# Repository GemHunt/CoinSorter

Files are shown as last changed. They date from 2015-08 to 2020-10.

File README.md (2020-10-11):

# CoinSorter

CoinSorter is a low cost, open source, coin inspection system. It sorts coins by solenoid, on conveyors, by classifying images with deep learning based models using [Caffe](https://github.com/BVLC/caffe), OpenCV, Python, LMDB, and Arduino. The system uses an algorithm in which coin designs and features can be found with 1-5 labeled examples. This is done by augmenting the training image set with many different camera and lighting angles. 

Check out the video (https://www.youtube.com/watch?v=cwcn3tuXrv4)

**CoinSorter is the main repo. The project has many sub-repos:**
* Conveyors: [conveyors repo](https://github.com/GemHunt/conveyors)
* Lighting: [lighting-augmentation repo](https://github.com/GemHunt/lighting-augmentation)
* Hopper Metering: [hopper-metering-tool repo](https://github.com/GemHunt/hopper-metering-tool)
* Inital Scanning & Operation: [real-time-coin-id repo](https://github.com/GemHunt/real-time-coin-id)
* SAIL: Unsupervised Labeling: [sail repo](https://github.com/GemHunt/sail)
* Caffe fork needed for SAIL: [caffe repo](https://github.com/GemHunt/caffe)

**The Goal of CoinSorter is to be a:**

* Image collection system for a stand-alone automated coin grading & counterfeit detection app
* High speed coin scanning, inspection, and sorting system
* Tool for finding rare coins
* Study tool for the classification of images using deep learning.
* System costing less than $200 as a kit excluding the cost of the computer and optional GPU card and less than $50 in a quantity of 20 systems provided you have free access to a laser cutter.
* Low cost, real world example of an open high speed machine vision system that can be used as a starting point for handling, inspection, and manufacture of other small parts.

|Clear Belt & Cameras Removed| Scanning with a Center Cutout| Top and Bottom Camera Closeup|
| --- | --- | --- |
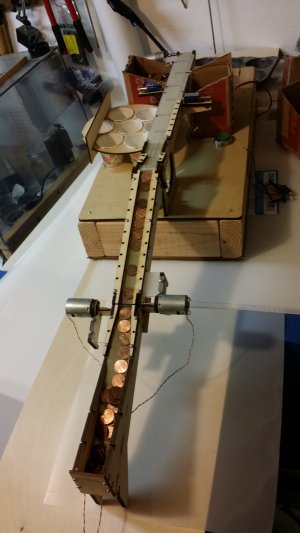
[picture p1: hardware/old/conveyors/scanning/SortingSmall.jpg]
Sorting
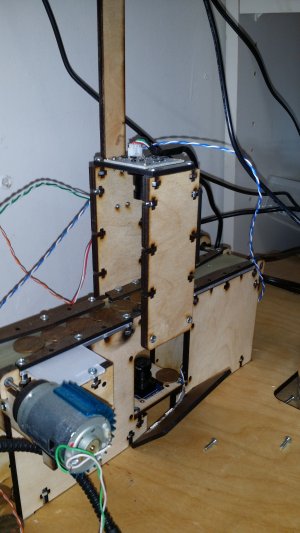
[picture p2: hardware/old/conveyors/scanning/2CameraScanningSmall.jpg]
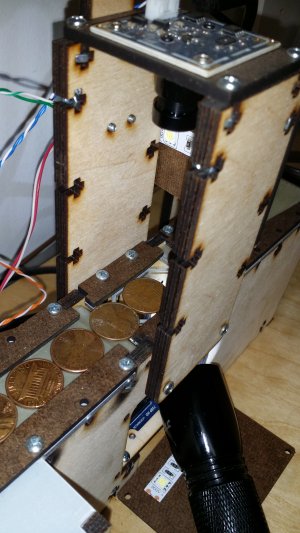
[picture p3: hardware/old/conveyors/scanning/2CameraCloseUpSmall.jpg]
||||

**Milestones & Short term goals & tasks:**
* GitHub milestones and issues are the best place to understand the project's past, present, and future. 
* In general the short term goal is to [sort 2 pennies a second by type, date and mintmark.](https://github.com/GemHunt/CoinSorter/issues/57)  
* Check out the [starting point issues](https://github.com/GemHunt/CoinSorter/labels/starting%20point) to see what is currently being worked on.
* For long term project direction [check out the issues for future milestones.](https://github.com/GemHunt/CoinSorter/milestones/Future%20Milestones) 

**Usage:**
* A new Python version is being planned.
* All C# code is being dropped from the project and will no long be maintained.   
* The new conveyors need to be documented and linked here, but in general everything is in [one Rhino 3D file.](https://github.com/GemHunt/CoinSorter/blob/master/hardware/conveyors/endMount/endMount.3dm)
* [View the old parts list and documentation](https://github.com/GemHunt/conveyors)

**How to Contribute & Participate**
* Buy and build the kit yourself. (I need to post the kit on eBay...)
* Work on, comment, and post new [issues.](https://github.com/GemHunt/CoinSorter/issues)
* If you have a laser cutter feel free to to build and sell systems yourself.
* If your into Caffe and don't want to post, just call me at 630-830-6640.

**Past Progress:**
* 2 working proof of concepts have been built proving Caffe & DIGITS is an excellent choice for coin image classification using small fully connected LeNet style networks.
* Over 20 prototype conveyors have been build each improving on the last design with around 150,000 coins imaged so far. 
* The full hardware setup is mature enough that others can start building and using it. 

**Detailed History:**
* The first proof of concept of this system used a C# project to capture images from a Canon Rebel camera and called MATLAB to preprocess them. A VB project was used to call DIGITS to classify the images and call a HP Power supply to drive a solenoid. These two projects have now been replaced. 

* The second proof of concept used C#, OpenCV, a webcam, Arduino solenoid control, and local classification with Caffe on Windows 10. Here is a [poster](https://github.com/GemHunt/CoinSorter/blob/master/docs/GTC%20Poster.pdf) and a [Power Point](https://github.com/GemHunt/CoinSorter/blob/master/docs/Deep%20Learning%20with%20Caffe%20%26%20DIGITS%20for%20Robotic.pptx) that describes the 2nd version. [You can download the second proof of concept release here.](https://github.com/GemHunt/CoinSorter/releases/tag/v0.2) 

* This first two groups of programs and scripts were just a quick proof of concept to show physical coin sorting. They sorted about 2 pennies a second, continuously. One solenoid and 2 physical bins are currently set up. Using Caffe it’s easy to distinguish between designs, orintation, and dates of coins. For example you can train a convolutional neural network (CNN, what Caffe uses) to determine if a coin image is heads vs tails or say recognize the state on a random US state quarter image. On one of the first models that was built Caffe could tell heads vs tails between US copper pennies 99.9% of the time. This can be done using using [DIGITS](https://github.com/NVIDIA/DIGITS) with default setting of AlexNet with no programming involved! In practice it's more efficient to use smaller image sizes and optimized networks. 

**In Review:**
* On the surface this system may look toy like and have a very narrow focus, but this is not true at all. You can take the basics of this system and use it for all sorts of very practical industrial uses. It’s not just sorting a handful of coins. It scales very quickly to tons of coins (or any parts for that matter). I have no doubt the system will get to the thousands of users range and be used for uses I could never envision. 

* Nothing remotely like it exists that is very low cost or open source. There are undocumented one off builds for all kinds of part handling. Probably the closest thing would be the open source pick and place machines. I have yet to see any personal or open source part handling systems that use the current crop of deep learning tools. MakerBot did have a conveyor on one of their machines, but this was a blind setup. Please let me know if you know about other, complete or not, documented open hardware machine vision systems

**Feel free to contact me if you have questions about this project.**

Thanks!  

Paul Krush

pkrush@Gemhunt.com

1-630-830-6640

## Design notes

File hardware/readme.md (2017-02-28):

This conveyor design is mostly for scanning. It's also to test out sorting. I have come to the conclusion that until conveyors are being build for sorting I don't know what they should look like. Initially scanning to learn how this all works is much different than deploying a conveyor to sort. 

The basic hardware of the conveyor is in the conveyors repo:https://github.com/GemHunt/conveyors

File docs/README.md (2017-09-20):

# CoinSorter

CoinSorter is an open source coin inspection system. It sorts coins by solenoid on conveyors by classifying images with models created using [Caffe](https://github.com/NVIDIA/caffe) &amp; [DIGITS](https://github.com/NVIDIA/DIGITS) and controlled with Python, OpenCV, and Arduino. 

**9/20/2017: This CoinSorter repo is out of date as new work is being doing in other repos. The project itself is still active. The biggest news is manual labeling has been eliminated! Designs and coin features sometimes can be found with only 1 example (One Shot Learning). The project has been rebuilt in a number of separate repos:**
* Conveyors: [conveyors repo](https://github.com/GemHunt/conveyors)
* Lighting: [lighting-augmentation repo](https://github.com/GemHunt/lighting-augmentation)
* Hopper Metering: [hopper-metering-tool repo](https://github.com/GemHunt/hopper-metering-tool)
* Inital Scanning & Operation: [real-time-coin-id repo](https://github.com/GemHunt/real-time-coin-id)
* SAIL: Unsupervised Labeling: [sail repo](https://github.com/GemHunt/sail)
* Caffe fork needed for SAIL: [caffe repo](https://github.com/GemHunt/caffe)

**The Goal of CoinSorter is to be a:**

* Image collection system for a stand-alone automated coin grading & counterfeit detection app
* High speed coin scanning, inspection, and sorting system
* Tool for finding rare coins
* Study tool for the classification of images using deep learning.
* System costing less than $200 as a kit excluding the cost of the computer and optional GPU card and less than $50 in a quantity of 20 systems provided you have free access to a laser cutter.
* Low cost, real world example of an open high speed machine vision system that can be used as a starting point for handling, inspection, and manufacture of other small parts.

|Clear Belt & Cameras Removed| Scanning with a Center Cutout| Top and Bottom Camera Closeup|
| --- | --- | --- |
|Sorting|Sorting|Sorting|

**Milestones & Short term goals & tasks:**
* GitHub milestones and issues are the best place to understand the project's past, present, and future. 
* In general the short term goal is to [sort 2 pennies a second by type, date and mintmark.](https://github.com/GemHunt/CoinSorter/issues/57)  
* Check out the [starting point issues](https://github.com/GemHunt/CoinSorter/labels/starting%20point) to see what is currently being worked on.
* For long term project direction [check out the issues for future milestones.](https://github.com/GemHunt/CoinSorter/milestones/Future%20Milestones) 

**Usage:**
* A new Python version is being planned.
* All C# code is being dropped from the project and will no long be maintained.   
* The new conveyors need to be documented and linked here, but in general everything is in [one Rhino 3D file.](https://github.com/GemHunt/CoinSorter/blob/master/hardware/conveyors/endMount/endMount.3dm)
* [View the old parts list and documentation](https://github.com/GemHunt/CoinSorter/tree/master/hardware/conveyors/conveyors.md) for the conveyors and the [old CAD files](https://github.com/GemHunt/CoinSorter/tree/master/hardware/conveyors/). 

**How to Contribute & Participate**
* Buy and build the kit yourself. (I need to post the kit on eBay...)
* Work on, comment, and post new [issues.](https://github.com/GemHunt/CoinSorter/issues)
* If you have a laser cutter feel free to to build and sell systems yourself.
* If your into Caffe and don't want to post, just call me at 630-830-6640.

**Past Progress:**
* 2 working proof of concepts have been built proving Caffe & DIGITS is an excellent choice for coin image classification using small fully connected LeNet style networks.
* Over 20 prototype conveyors have been build each improving on the last design with around 150,000 coins imaged so far. 
* The full hardware setup is mature enough that others can start building and using it. 

**Detailed History:**
* The first proof of concept of this system used a C# project to capture images from a Canon Rebel camera and called MATLAB to preprocess them. A VB project was used to call DIGITS to classify the images and call a HP Power supply to drive a solenoid. These two projects have now been replaced. 

* The second proof of concept used C#, OpenCV, a webcam, Arduino solenoid control, and local classification with Caffe on Windows 10. Here is a [poster](https://github.com/GemHunt/CoinSorter/blob/master/docs/GTC%20Poster.pdf) and a [Power Point](https://github.com/GemHunt/CoinSorter/blob/master/docs/Deep%20Learning%20with%20Caffe%20%26%20DIGITS%20for%20Robotic.pptx) that describes the 2nd version. [You can download the second proof of concept release here.](https://github.com/GemHunt/CoinSorter/releases/tag/v0.2) 

* This first two groups of programs and scripts were just a quick proof of concept to show physical coin sorting. They sorted about 2 pennies a second, continuously. One solenoid and 2 physical bins are currently set up. Using Caffe it’s easy to distinguish between designs, orintation, and dates of coins. For example you can train a convolutional neural network (CNN, what Caffe uses) to determine if a coin image is heads vs tails or say recognize the state on a random US state quarter image. On one of the first models that was built Caffe could tell heads vs tails between US copper pennies 99.9% of the time. This can be done using using [DIGITS](https://github.com/NVIDIA/DIGITS) with default setting of AlexNet with no programming involved! In practice it's more efficient to use smaller image sizes and optimized networks. 

**In Review:**
* On the surface this system may look toy like and have a very narrow focus, but this is not true at all. You can take the basics of this system and use it for all sorts of very practical industrial uses. It’s not just sorting a handful of coins. It scales very quickly to tons of coins (or any parts for that matter). I have no doubt the system will get to the thousands of users range and be used for uses I could never envision. 

* Nothing remotely like it exists that is very low cost or open source. There are undocumented one off builds for all kinds of part handling. Probably the closest thing would be the open source pick and place machines. I have yet to see any personal or open source part handling systems that use the current crop of deep learning tools. MakerBot did have a conveyor on one of their machines, but this was a blind setup. Please let me know if you know about other, complete or not, documented open hardware machine vision systems

**Feel free to contact me if you have questions about this project.**

Thanks!  

Paul Krush

pkrush@Gemhunt.com

1-630-830-6640

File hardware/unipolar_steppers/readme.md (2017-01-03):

Mitsumi m25sp-5n Unipolar Step Sequence
White:Orange:Red:Blue

This motor came from Jameco.
There is a tiny circuit board on the motor that you can cut the trace to power this with a bipolar driver. 

Notes to ordering better steppers:
Order bipolar wired motors
The 2 hole flange is much better for changing out motors, then the 370/385 DC motor style. 
These have a 5mm shaft. 8-10mm would be better. 
Have 4 stripped & tinned wires soldered on with assorted lengths.

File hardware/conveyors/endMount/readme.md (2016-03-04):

Conveyor Build Instructions

**Laser Cutting Tips:**
Push parts out from top (clean) side?
Rotating to top view is least confusing 
Mirror the side rail when cutting. 
Standard way to rotate to top views: 
	If you want to mirror flip the angle. 
If drawings are in Right view:
In front view, rotate, c    20, 0    90    enter - enter
If drawings are in Front view
In right view, rotate, c    0, 0    -90    enter - enter
Then invert & change object layer

Assembly Tips:
Nuts go into the clean (non-charred) side better. 
Motor & solenoid have M3 8mm screws
Horizontal solenoid plate screws & guide screws are 5/8” 4-40
Finger guides are 4# 3/8” sheet metal screws for now. 
All other screws are ½” 4-40.

If a nut gets stuck squeezing between 2 coins helps. 
Only snug screws until everything it together, then finish tightening. 

Make a Belt:
The glossy side should be the inside on the belt. The mat side is stickier. 
Cut 30mm wide belt:
	20cm Feeder/scanner Conveyor
	22cm short conveyor
	44.5cm hopper & accumulator conveyors
	104cm scanning conveyor

Heat seal (bond) smooth side in (Bright lighting helps)
I use an 8" $25 heat sealer for poly bags with a 2mm element.(3mm would be better)(A custom bonding rig would be nicer).
Scotch tape a 1mm overlap. 
Turn it inside out so the tape side is opposite the heating element before heat sealing. 
Heat seal 2 times to get the both side of the 1mm whole seam for .3mm thick
Heat seal 1 time for .15mm thick 
	On the dial I use a 2 setting for 0.15mm and 4.5 setting for 0.3mm
Remove Tape
Try not to heat seal a single layer area as this will thin it out. 
The clear belting is sticky. I sand all top plates with 220 sand paper. I wounder what grit is the best. 

Assembly Instructions:
	Put the 58mm shaft on the motor:
	Add the 17mm tubing coupling to the motor shaft. 
	Press 7mm on the motor (most of the way) 
	Add the 58mm 2mm shaft to this tubing, pressing about 7mm on. 
	There should be about a 2mm of tubing in the middle. 
Mount the motor:
To the Motor Rail 
With M3x.5 x 8mm long screws.
Cleaner side to the motor face. 
Screw on top plate to motor rail
Add solenoid plate to motor rail with one 5/8” screw
Add Middle Rail to top plate with 2 screws

Change this: it’s easier to then put on shafts, then belt, then side rail. 

If using guides:	
Add them with three 5/8” screws instead of two ½” screws
Guides need shim washers between the top plate and the guide
Add Side Rail to top plate with 2 screws
If using guides:	
Add them with three 5/8” screws instead of two ½” screws
Guides need shim washers between the top plate and the guide
Tighten guides with guide spacer in-between. 
Add shorter 42mm long 2mm shaft with 3/16 spacer pulleys:
	2 longer spacers on the end, and one shorter spacer in the middle. 
Put the belt on.
Add motor end plate
Add end plate
Final screw tightening:
Squeeze the side rails together when tightening the end plates. 
Don’t tighten top plate super tight as it will crown. 

Belt change:
Take off the end plates. 
Find a way to make it so you don’t have to take off the end plates? 
3 ½ minutes to change the belt with taking the end plates off. 
Squeeze the side rails together when tightening the end plates.

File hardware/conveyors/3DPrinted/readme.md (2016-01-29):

I don't think I will use this 3D Printed style again. The laser cut version is simpler and quicker to make. 

**Three types of conveyor ends have been used successfully:**
* Motor end in ¾” MDF
* Pulley end in ¾ MDF
* Pulley end in ¼ MDF

These conveyors built from ¾” frames have turned out way better than I thought they would. I first used 1mm thick belting at 100RPM and this was a bit under-powered. All the power is used to move the thicker belt under tension. It would move a full gallon of milk(3+ kilos) with no issues. 

With the 0.15mm thick belting that is currently be used the motors can be smaller, especially if you put in ball bearings. 

**Motor end in ¾” MDF Parts:**
* 25MM Gear motor, 4mm shaft 100-1000RPM
* 2 motor mount screws: M3-0.5 6 mm screws
* 3D printed gearbox bracket
* 3D printed D-coupling to take motor 4mm ID “D” to ¼” OD
* Coupling: Polyurethane Tubing, ½” OD, ¼” ID. 
* Coupling: Zip/cable Ties: 4”
* 75mm long ¼” steel shaft
* 35 mm long 3D printed pulley. 22mm diameter. 
* Drilled with “D”0.246” drill to press fit on ¼” shaft
* 2 3D printed Pulley Holders. 
* 2 Bushings: stock nylon shoulder spacers ½” Long, ¼” ID, 5/16” ID, ½” ID Flange
* 3 8” zip/cable ties hold on the gearbox bracket & pulley holders

**Pulley end in ¾ MDF**
* Same as motor side, except 60mm long shaft. 

**Pulley end in ¼” MDF:**
* Pulley end ¼” is 60mm wide
* 1/8” steel shaft, 60mm long
* 4 ¼” diameter nylon spacers, 1/8” hole, ½” long, Center spacer has tape to make it crown. 
* Wood is cutout for the pulleys
* Remaining wood is drilled 1/8”
* It’s pretty crude and fragile, but once it starts working I have yet to see fail. 
* It’s easy to drill so the shaft is not straight. Then the belt walks to one side. 
* In the pictures below the belt walked to one side anyway. It just did not matter. 

**Conveyor Belt:**
* 30mm wide, 0.15mm thick Polyurethane
* Normally used for sealing fabric together, under garment strapping, etc.
* Sold as “TPU Tape” on Aliexpress.com
* Length wise sized 5% under  
* Bonded together with a standard impulse heat sealer used for sealing poly plastic bags. 

**Speed Controllers:**
* The first proof of concept had 24V power stepped down to 5 to 18 volts for the 12V motors with DC-DC LM2596 modules. This are really common, $1-2 on eBay, Amazon, etc. The system moving coins with motors running at 5-7 volts is surprisingly quiet with the coin hopper turned off. 

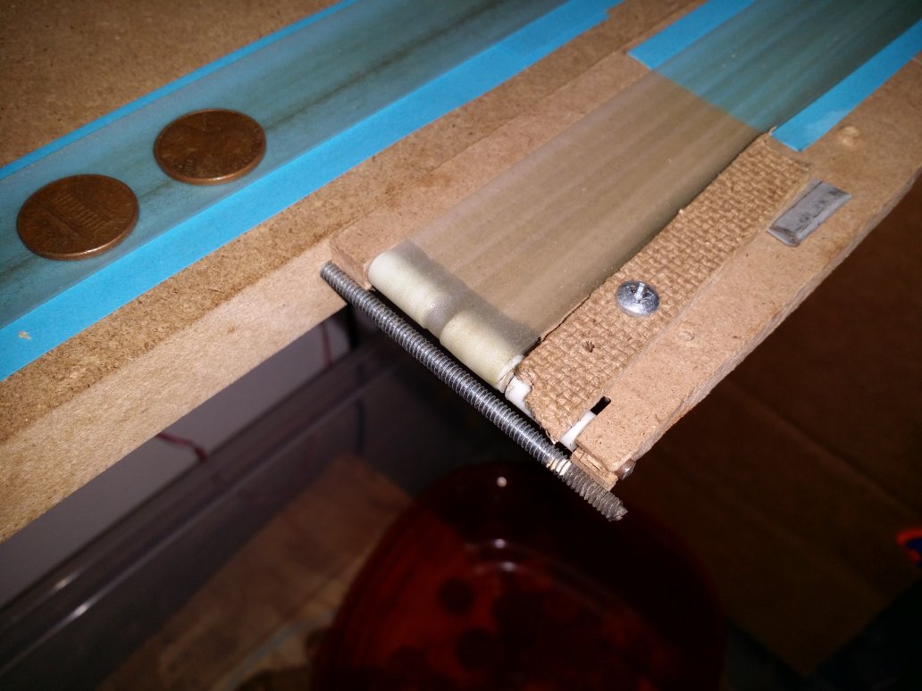
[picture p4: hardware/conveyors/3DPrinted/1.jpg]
Image of Conveyor 1

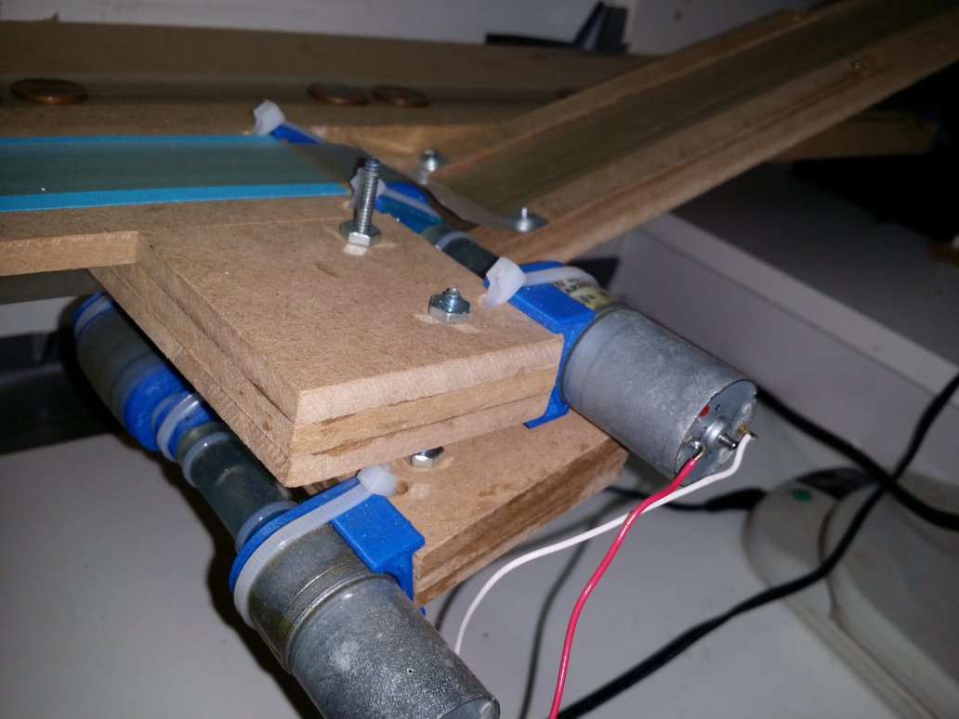
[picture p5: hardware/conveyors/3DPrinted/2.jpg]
Image of Conveyor 2

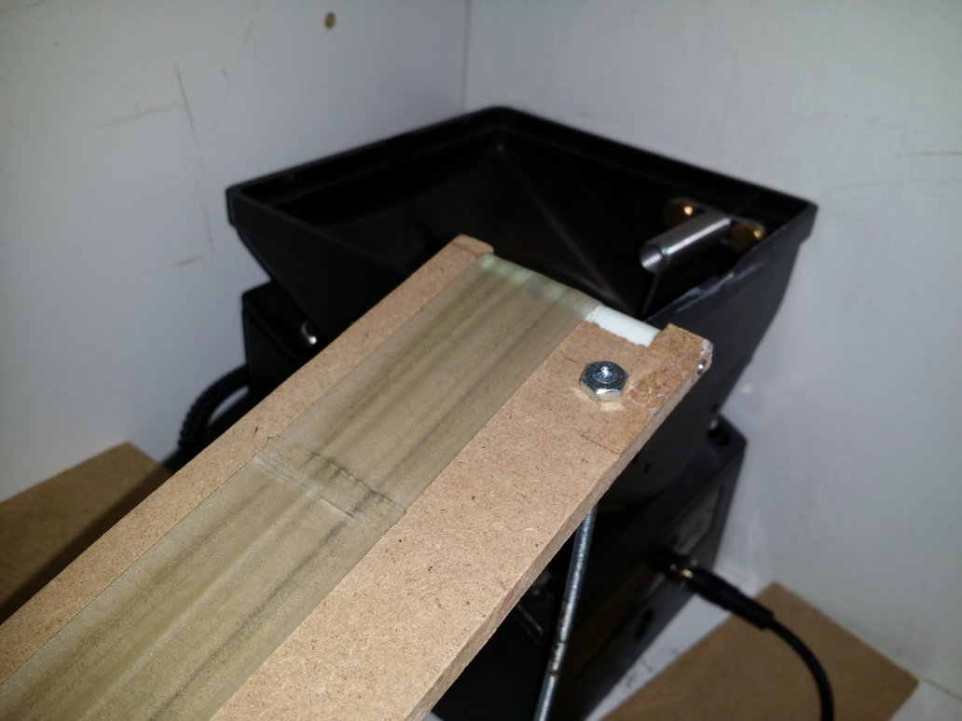
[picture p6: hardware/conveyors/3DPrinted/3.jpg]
Image of Conveyor 3

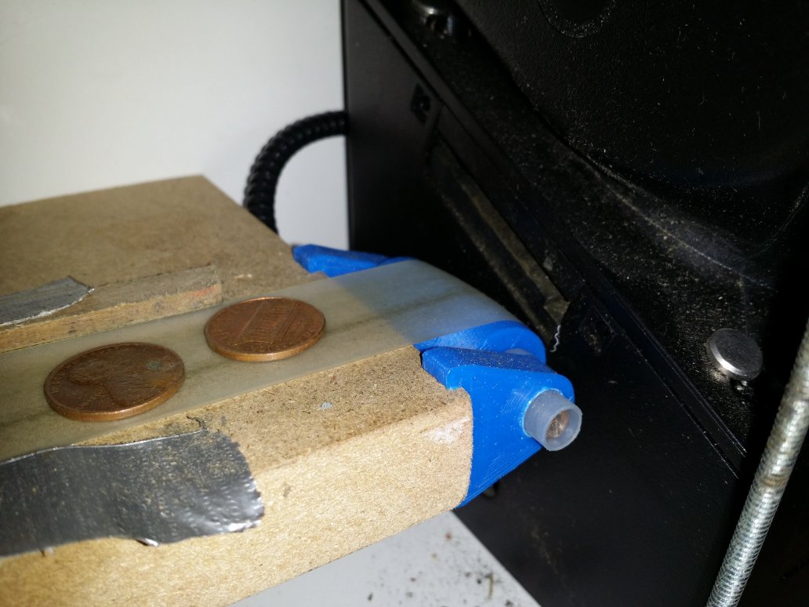
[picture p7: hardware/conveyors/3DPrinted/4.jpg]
Image of Conveyor 4

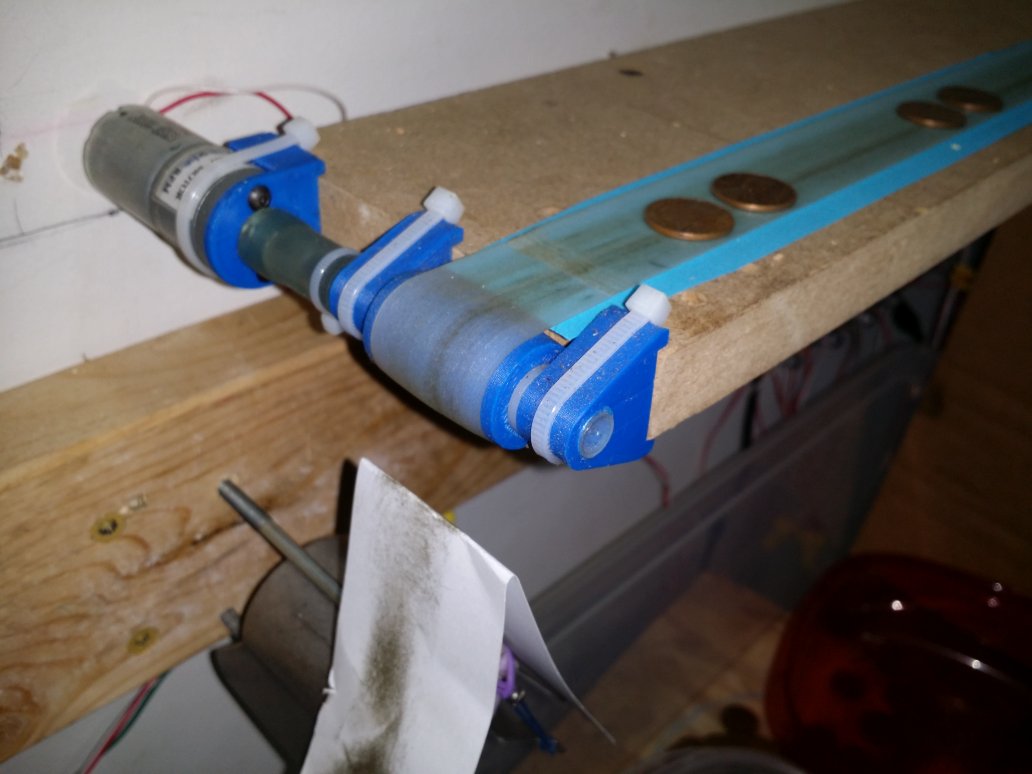
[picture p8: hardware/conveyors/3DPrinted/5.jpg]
Image of Conveyor 5


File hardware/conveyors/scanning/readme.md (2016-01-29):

This is the start of the scanning conveyor

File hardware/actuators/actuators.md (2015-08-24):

**Proof of Concept Actuator:**

A Rotary Flapper Solenoid:
* A USPS surplus RAM MFG CO ROTARY SOLENOID ACTUATOR part 40R10102
* This is too big and I don't recommend it. 

What should be used?
Solenoids certainly seems the most logical.
Such as low cost push solenoids to knock coins off the belt:
* 5mm travel?
* Maybe some type of foot it's more then just the rod end, but try without a foot first.
* Rotary solenoids seems like a good idea, but I have not seen many.

Motors you could sort to more than one bin:
* RC servos are so common and easy to control. 
* Cheap stepper motors might not be a bad idea.

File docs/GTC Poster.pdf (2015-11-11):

# High Speed Coin Sorting With Convolutional Neural Networks

# Paul Krush

https://github.com/GemHunt/CoinSorter

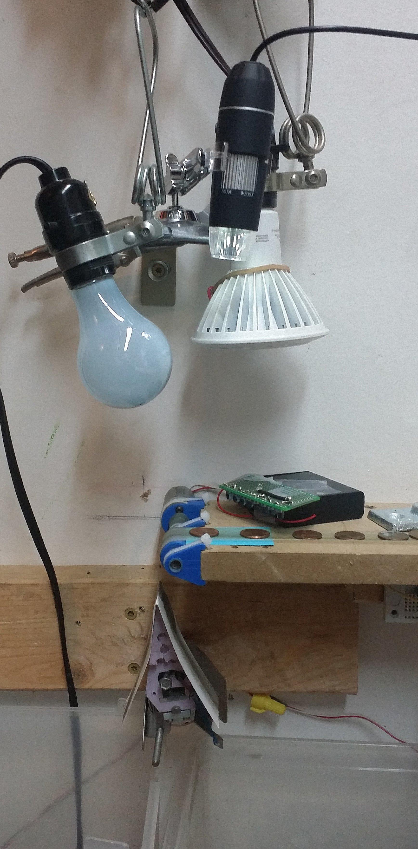
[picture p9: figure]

## Introduction:

The goal of this project is to physically sort pennies by date very quickly with low cost open source hardware & software.

Caffe CNN: Coin date classification, a stock cifar10 network, 32x32 color

Caffe CNN: Coin orientation classification (images rotated to create 360 different categories) LeNet with an additional set of conv & pooling layers, 2x output, 64x64 gray

Caffe CNN: Coin design classification (Heads vs Tails vs Other…) LeNet with an additional set of conv & pooling layers. 2x output, 60x60 gray, 12x rotational augmentation

Caffe CNN: Detection of the 5% poorly cropped coins with a stock cifar10 network, 32x32 color

OpenCV: Coin image crop from contour detection

OpenCV: Threshold in Cr component of the YCbCr space

OpenCV: Removal of skew (caused by coin moving at high speed)

OpenCV: Image captured from webcam, triggered by IR sensor from Arduino

## Image Processing Pipeline:

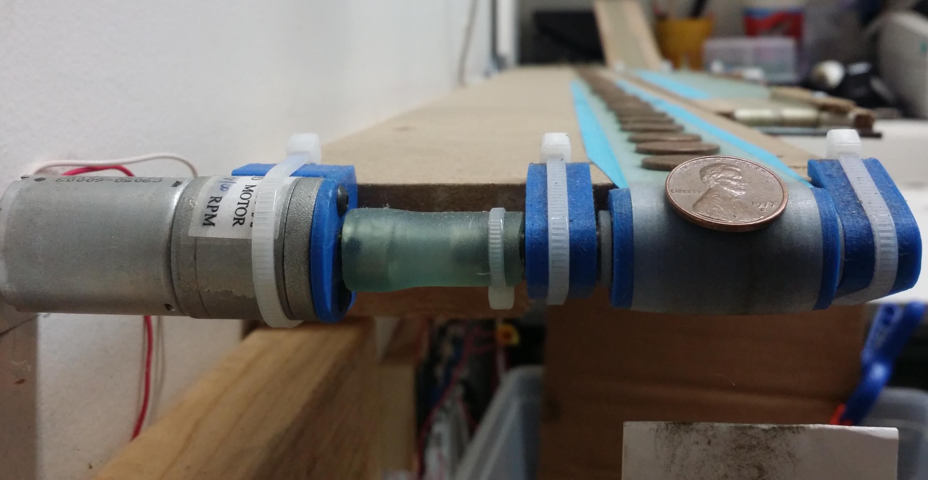
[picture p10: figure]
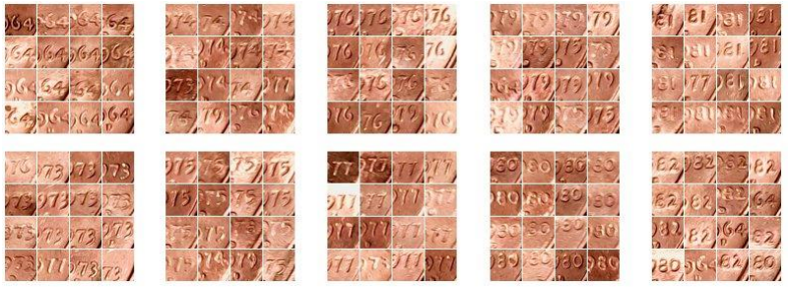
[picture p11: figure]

## Future Work:

One of the holy grails of modern numismatics is to discover new types of coin varieties and mint-made errors. Automatically correlating coin regions and features by date and mint mark is the next logical milestone to archive this. Capturing both sides of the coin will be a requirement to do this.

## Next Steps:

Camera & lighting
needs to be fixtured
and standardized.
Four different lighting
and camera setups
have been used so far.
Accuracy drops
drastically after the
camera type, position,
lens, or lighting
changes. Cropping
issues need to be fixed
and matched to the
possible new camera.

## Motivation:

To learn about machine vision and get experience with the full life cycle of a machine vision product. To gain experience with the current crop of deep learning tools and their use of NVidia GPUs.
So the tail wags the dog… The field of high speed coin classification was chosen because of current GPU computational efficiency over CPUs and more importantly future GPU computational scalability.

## Hardware & Software Mechanics:

At this point the system is just a quick proof of concept to show physical coin sorting. It sorts about 2 pennies a second, continuously. One solenoid and 2 physical bins are currently set up. It uses C#, OpenCV for image preprocessing, a cheap microscope webcam, an Arduino for solenoid control, SQLite, and local classification with Caffe complied on Windows 10. Model training is done on a Linux server, either local or AWS, with Caffe & DIGITS.
Coins are metered by an off-the-shelf coin hopper. Conveyor hardware is 3D printed ABS. Conveyor belting is undergarment strapping. (0.15mm “TPU Tape”)

## Results:

Start to finish preliminary accuracy is around 70 percent. Expected accuracy is much higher. Most of the error at this point is due to using a very small training set. Simple improvements can be made throughout the pipeline.

## Conclusion:

So far accuracy is higher than expected which is great. Unfortunately the project is taking a lot longer than expected. Computational requirements are much lower than expected, which ironically does not fulfill the stated goal of needing a GPU for classification! Of course this is a good problem to have and leaves the door wide open for more complex work in the future.

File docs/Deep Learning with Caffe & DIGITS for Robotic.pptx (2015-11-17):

## Deep Learning with Caffe & DIGITS for Robotic Coin Collecting

https://github.com/GemHunt/CoinSorter

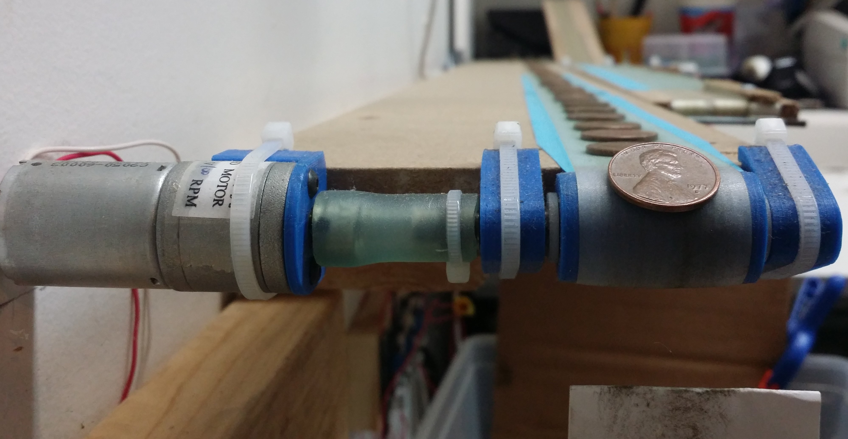
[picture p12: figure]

## Who am I?

- Software developer and mechatronics engineer
- Mechatronics?
- GemHunt.com: Am I going the startup route? Again?
- Live Carol Stream with my wife and two boys

## Questions? Comments? Feel free to Stop me! Or just Post a GitHub issue github.com/GemHunt/CoinSorter

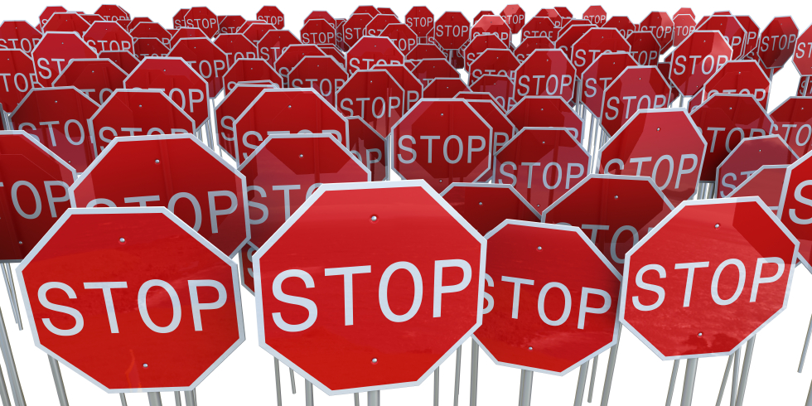
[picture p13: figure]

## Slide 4

Start Time | Minutes
7:00 PM | 10 | UniForum Intro
7:10 PM | 5 | Presentation Intro
7:15 PM | 5 | Check out the GitHub: Project Goals/Milestones
7:20 PM | 5 | What is Deep Learning?
7:25 PM | 5 | What is Caffe/Digits?
7:30 PM | 10 | Installing Caffe & Digits (AWS/Windows)
7:40 PM | 15 | Using Digits
7:55 PM | 10 | CoinSorter pipeline & Issues
8:05 PM | 10 | Results / Demo of the second version
8:15 PM | 10 | Next Steps/ Issues/ Future
8:25 PM | 35 | Questions

## First, Lets check out The Last Version

- https://www.youtube.com/watch?v=_fJcIxWgQbs

## What Is this all about?: Finding Pennies Coins by Date

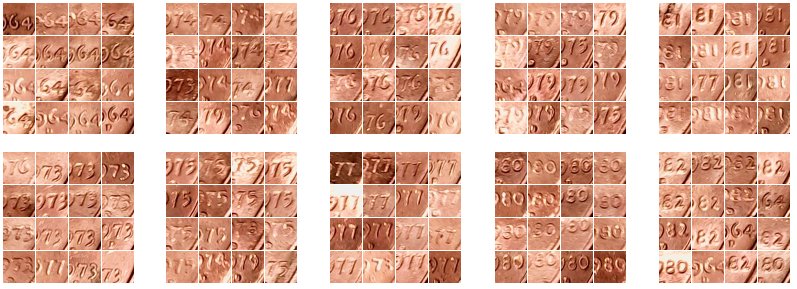
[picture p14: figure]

## Why I am doing this?

- A step to discover new types of rare coin varieties and mint-made errors
- To learn about machine vision & machine learning
- Because it’s newly scalable in many different ways
- To make $$$? Maybe. More importantly to open doors I didn’t know existed.

## Head over to https://github.com/GemHunt/CoinSorter

## What is Deep Learning?

- From Wikipedia: Deep learning is a branch of machine learning based on a set of algorithms that attempt to model high-level abstractions in data by using multiple processing layers with complex structures or otherwise, composed of multiple non-linear transformations.
- Backup? What is machine learning?
- Creating a tool to classify data without explicitly telling the computer how to.
- Either by giving similar data (Supervised)
- Or by some form of grouping (Unsupervised)
- CoinSorter is mostly supervised…

## Again, What is Deep Learning?

- Most popular example: Supervised classification of images
(using pre-labels images to find more like them)
- High level tool with no programing
- Using Neural networks
- Trained On GPUs
- A buzz word for something that has existed for a long time, but for a number of reasons has started really taking off.
- Caffe, Torch, Theano are the big three libraries
- http://cs.stanford.edu/people/karpathy/convnetjs/

## What is Caffe & Digits?

  - Caffe: (https://docs.google.com/presentation/d/1UeKXVgRvvxg9OUdh_UiC5G71UMscNPlvArsWER41PsU/edit)
  - https (https://docs.google.com/presentation/d/1UeKXVgRvvxg9OUdh_UiC5G71UMscNPlvArsWER41PsU/edit)://docs.google.com/presentation/d/1UeKXVgRvvxg9OUdh_UiC5G71UMscNPlvArsWER41PsU/edit#slide=id.gc2fcdcce7_216_ (https://docs.google.com/presentation/d/1UeKXVgRvvxg9OUdh_UiC5G71UMscNPlvArsWER41PsU/edit)
  - NVIDIA’s DIGETS is a web based front end to Caffe.
    - We will see a lot more in a bit…

## Installation & Setup of Caffe & digits

Checkout: https://github.com/GemHunt/CoinSorter/blob/master/scripts/AWSCaffeDigetsBuild.md

## Using Digits

- Using sets of images to train models.
- Jump some of the details to introduce DIGITS…
- …then we will come back and put it all together.

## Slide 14

OpenCV: Image captured from webcam, triggered by IR sensor from Arduino
OpenCV: Removal of skew (caused by coin moving at high speed)
OpenCV: Threshold in Cr component of the YCbCr space
OpenCV: Coin image crop from contour detection
Image Processing Pipeline:

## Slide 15

OpenCV: Coin image crop from contour detection
Caffe CNN: Coin date classification, a stock cifar10 network, 32x32 color
Caffe CNN: Coin orientation classification (images rotated to create 360 different categories) LeNet with an additional set of conv & pooling layers, 2x output, 64x64 gray
Caffe CNN: Coin design classification (Heads vs Tails vs Other…) LeNet with an additional set of conv & pooling layers. 2x output, 60x60 gray, 12x rotational augmentation
Caffe CNN: Detection of the 5% poorly cropped coins with a
stock cifar10 network, 32x32 color

## Image Processing Pipeline In C++

- Check out model folders and C++ code: (https://github.com/GemHunt/CoinSorter/blob/master/windowsCppSource/classification.cpp#L249)
- https://github.com/GemHunt/CoinSorter/blob/master/windowsCppSource/classification.cpp#L249

## Demo of live system

- Test lights more durable than thought
- Cause skew by hand
- Obscure date
- Try different rotations on rare dates

## Next Steps

- https://github.com/GemHunt/CoinSorter/milestones/Future%20Milestones

## Questions & Comments

- Post an issue at:
- https://github.com/GemHunt/CoinSorter
- Or email me at:
- pkrush@gemhunt.com

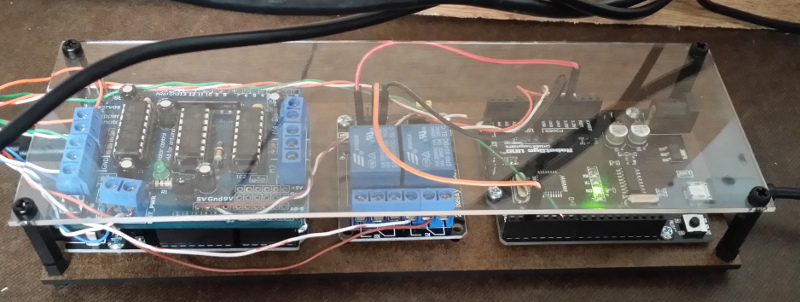
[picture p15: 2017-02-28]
hardware/controls.jpg

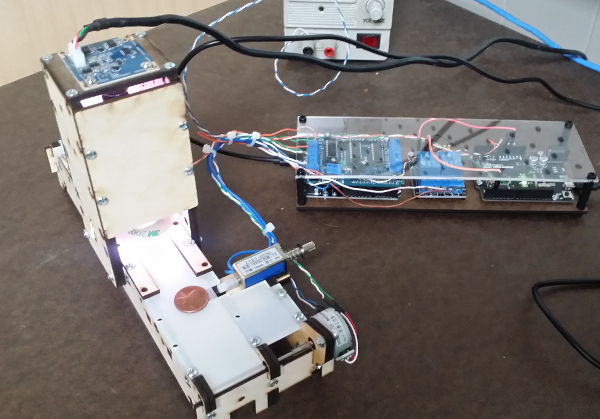
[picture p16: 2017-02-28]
hardware/scanner-conveyor.jpg

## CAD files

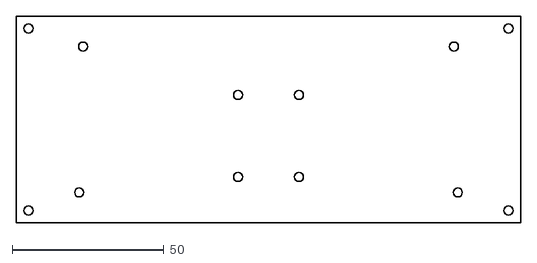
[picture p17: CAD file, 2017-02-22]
2-arduino-enclosure/2-arduino-enclosure.dxf
166.2 x 68.0

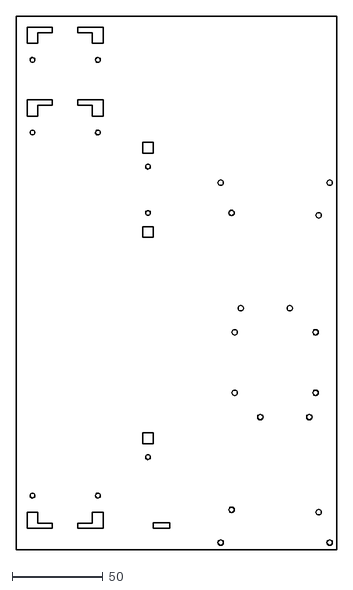
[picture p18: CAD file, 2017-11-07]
hardware/2-arduino-enclosure/base-plate.dxf
176.6 x 293.8

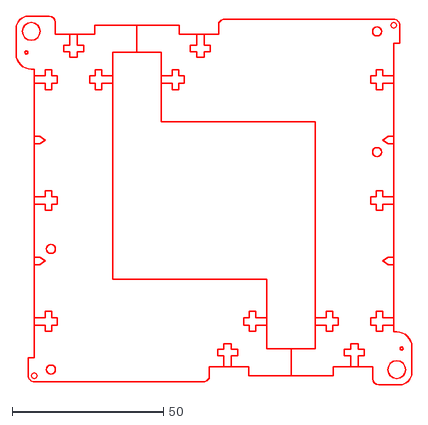
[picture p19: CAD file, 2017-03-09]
hardware/2-arduino-enclosure/temp/6mm.dxf
131.0 x 122.0

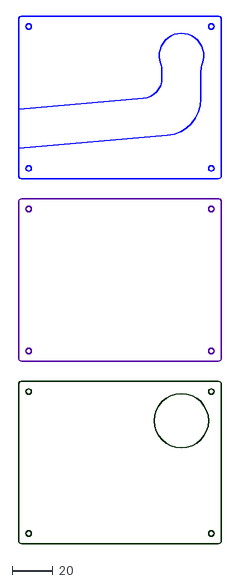
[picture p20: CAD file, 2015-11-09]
hardware/coinAcceptor/coinAcceptor.dxf
100.0 x 260.0

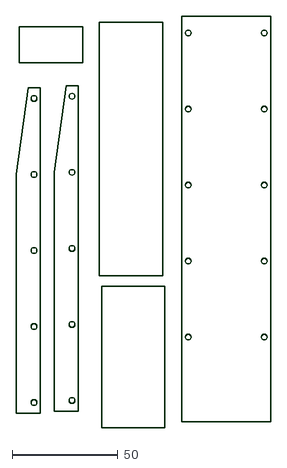
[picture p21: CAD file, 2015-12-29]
hardware/conveyors/conveyorFrame/3mm.dxf
120.3 x 195.0

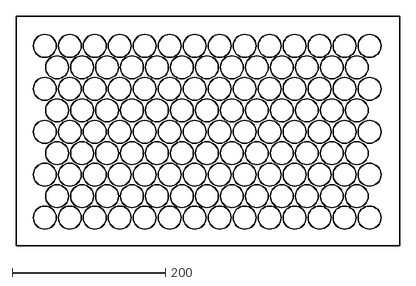
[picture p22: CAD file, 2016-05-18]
hardware/conveyors/endMount/3mm.dxf
500.0 x 300.0

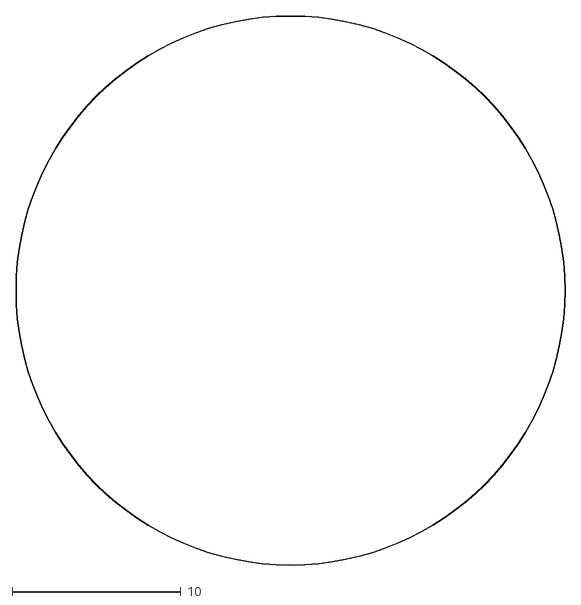
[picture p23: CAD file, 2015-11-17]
hardware/frame/32.5.dxf
32.5 x 32.5

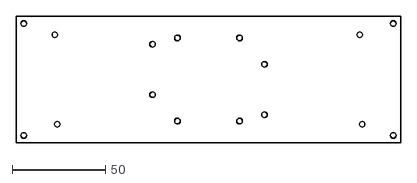
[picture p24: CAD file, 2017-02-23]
hardware/scanner-sorter/2-arduino-enclosure/2-arduino-enclosure.dxf
206.2 x 68.0

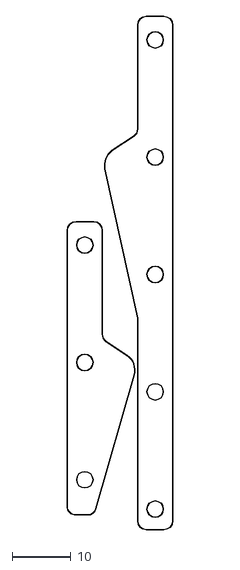
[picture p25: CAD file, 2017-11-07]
hardware/2-arduino-enclosure/camera-guides2.dxf
18.0 x 87.5

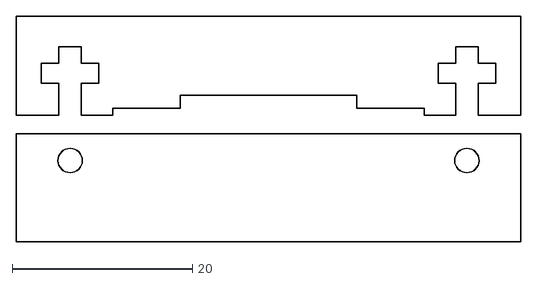
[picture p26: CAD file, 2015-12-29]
hardware/conveyors/conveyorFrame/blocker.dxf
56.0 x 25.0

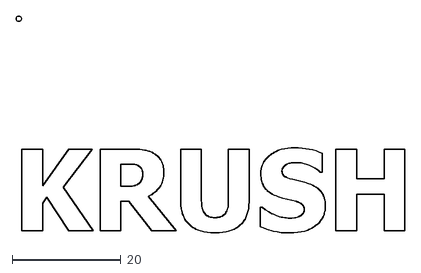
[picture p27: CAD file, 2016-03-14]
hardware/conveyors/endMount/0.2mm.dxf
71.5 x 39.9

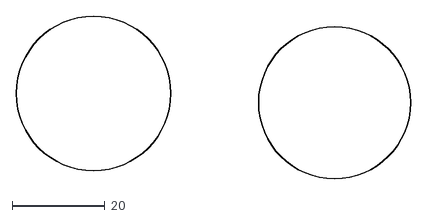
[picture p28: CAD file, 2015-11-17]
hardware/frame/TestHoles.dxf
85.1 x 35.0

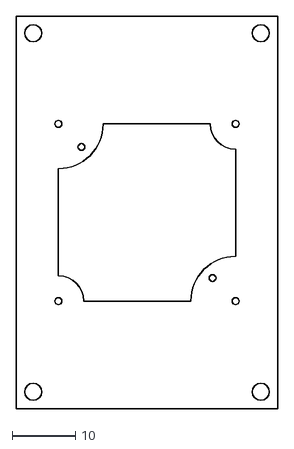
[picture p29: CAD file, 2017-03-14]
hardware/2-arduino-enclosure/camera-mounting-plate2.dxf
41.4 x 62.0

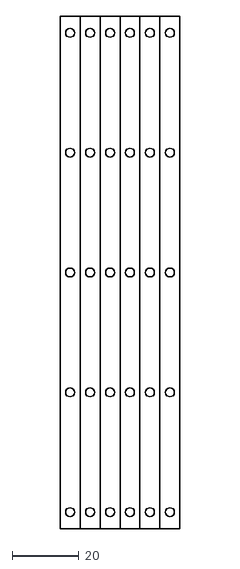
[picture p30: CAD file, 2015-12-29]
hardware/conveyors/0.2mm.dxf
36.0 x 154.0

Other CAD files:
hardware/conveyors/endMount/2mm.dxf
hardware/frame/frameTopTest.dxf
hardware/2-arduino-enclosure/camera-cover3.dxf
hardware/conveyors/endMount/6mm.dxf
hardware/2-arduino-enclosure/camera-cover.dxf
hardware/2-arduino-enclosure/camera-cover2.dxf
hardware/2-arduino-enclosure/camera-guide-washers.dxf
hardware/2-arduino-enclosure/camera-guides.dxf
hardware/2-arduino-enclosure/camera-mounting-plate.dxf
hardware/2-arduino-enclosure/camera-side-rail.dxf
hardware/2-arduino-enclosure/camera-side-rail2.dxf
hardware/2-arduino-enclosure/clear-control-cover.dxf
hardware/2-arduino-enclosure/motor-rail-25by-stepper.dxf
hardware/2-arduino-enclosure/sideRail.dxf
hardware/2-arduino-enclosure/slide.dxf
hardware/2-arduino-enclosure/temp/temp.3dm
hardware/2-arduino-enclosure/top-plate.dxf
hardware/actuators/EnglishTest/englishTest.3dm
hardware/coinAcceptor/coinAcceptor.3dm
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

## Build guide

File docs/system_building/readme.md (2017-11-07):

This folder has documention on building and configuring caffe on single machines and aws. It's somewhat out of date. 

As far as I know no one has built CoinSorter...

At this point just call me if you want to try to build it! 1-630-830-6640 I will try to work you through it. 

Tasks to make a build easier:

* Remove hardcoded directories, and add a configuration file
* Add a fake camera, solenoid, and raw image database so the software can be run without any special hardware
* Try to build on a different machine and document this
* Build again on AWS and make a public AMI for this
* Finish BuildInstructions.md

* Add a note to the README; something like this:

*Please fork me: This system is at the point that you could build the hardware and do this yourself. Most likely you will have to build new models from your cameras images. Also, there is a test mode that you can use the system without a camera or solenoid controller. You should be to clone or fork release 0.2 and get this system to work with the release 0.2 images and models out on GemHunt.com. Its rather difficult to compile this, as there is a huge C++ DLL project and a C# project.  Click here for build instructions. Or you cheat: I built this already on AWS and made a Public Windows AMI. Also click here for the Linux Training Server AMI.*

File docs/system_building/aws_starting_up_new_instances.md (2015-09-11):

```
#1.) Attach your EBS Volume after starting your instance. 
#2.) Mount the Existing volume
sudo mount /dev/xvdf /data

#gets rid of Failed to initialize libdc1394
sudo ln /dev/null /dev/raw1394

#3.) Start the DIGITS server:
./digits/digits-devserver

#4.) If FTP Needed:   Open the FTP config for editing:
sudo vi /etc/vsftpd.conf

#Change pasv_address to the Public IP of the AWS Instance:
pasv_address=54.157.133.214
#Change password:
sudo passwd ubuntu
#Restart server for changes to take effect:
sudo service vsftpd restart

#Shuting down:
sudo umount -d /dev/xvdf
```

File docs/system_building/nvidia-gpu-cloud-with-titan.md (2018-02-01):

nvidia-gpu-cloud-with-titan

This is my notes the second time I tried this. There is still a permissions issue with Docker.

Once the server is set up the promise of a 5 minute install holds true, but you still need to know the basics of using Docker. 

**Installation notes beyond what is documented:**
* Starting with:
* http://docs.nvidia.com/ngc/ngc-titan-setup-guide/index.html
* Burn 16.04.3 Desktop AMD64 Aug 2017 ISO to DVD
* (They really should state the exact ISO to pull.) 
* https://download.docker.com/linux/ubuntu/dists/xenial/pool/stable/amd64/
* With a single NVIDIA TITAN Xp collectors edition installed
* Boot & Install Ubuntu:
* Don’t check the boxes for “download updates or install third party software”
* Force UEFI Installation:click “Go Back” 
* “Erase Disk and install Ubuntu”: Install Now
* On first start up make sure 4.10 kernel is running:
* uname -a

* Follow the directions at:
* http://docs.nvidia.com/ngc/ngc-titan-setup-guide/index.html
* Make script files by copying out of Firefox(Chrome copies wrong)
* Don’t run sudo apt-get update until things don’t work
* Don’t use sudo until things don’t work

**Using Nvidia GPU Cloud with Titan Usage:**
* mkdir ngc
* cd ngc
* mkdir digits
* There is an issue that I have to use sudo and I have to manually start the daemon
* start the docker Daemon: 
* sudo dockerd
* sudo docker login -u '$oauthtoken' --password-stdin nvcr.io <<< 'Qt4M2VkL---------Your API KEY -------3ZGZZmNIw'
* sudo docker pull nvcr.io/nvidia/digits:18.01
* sudo nvidia-docker run -it --rm --net=host --name digits -v /data:/data -v /digits-jobs:/workspace/jobs nvcr.io/nvidia/digits:18.01
* In a new terminal open a shell inside the workspace:
* sudo docker exec -it digits /bin/bash
* To show the base directory for the frameworks inside the container:
* cd /opt/ | ls
* To show the binaries the container has:
* cd/usr/local/bin

***********************************************************************************
**Docker tasks for myself**
* Write a script to start a container on system startup
* Fix the permissions issue 

**Docker notes for myself:**
* https://ngc.nvidia.com
* http://docs.nvidia.com/ngc/ngc-user-guide/index.html
* https://github.com/NVIDIA/nvidia-docker/wiki/
* https://hub.docker.com/r/nvidia/
* https://github.com/NVIDIA/nvidia-docker/wiki/Third-party
* Why does nvidia sometimes say nvidia-docker or just docker:
* nvidia-docker only modifies the behavior of the run and create Docker commands
* http://phase2.github.io/devtools/common-tasks/ssh-into-a-container/

**Docker commands**
* start the docker Daemon: sudo dockerd
* List containers:
* sudo docker ps
* Shell into container:
* sudo docker exec -it digits /bin/bash
* Use the ID from “docker ps” or name the container when you run it.

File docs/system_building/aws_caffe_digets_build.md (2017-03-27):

I have used this many times at this point:

1.) I(Paul Krush) started with this, by Raffael Vogler:
GPU Powered DeepLearning with NVIDIA DIGITS on EC2:
http://www.joyofdata.de/blog/gpu-powered-deeplearning-with-nvidia-digits/

2.) I rebuilt for Digits 2.

3.) I then rebuilt for cudnn3 and Nidvia Caffe v0.13.0 
	This one took me about 2 hours
	
4.) Then I built a local server. (9/22/2015)
	MSI H81M-E33 motherboard, Intel G3258 Processor, 8GB of Ram, 250GB SSD, GTX 970
	It really was the same as AWS except for installing ubuntu 14.04
	Changes AWS or Local:
		cuDnn is now "prod" (not rc) 
		cuda 7.5 is now installing by default
		udo was needed before Caffe requirements
5.) Rebuilt the same hardware (6/9/2016)  	
	ubuntu 14.04(Still recommended by Nvidia), CUDA 8RC, CuDnn 5.0 
	Digits is claiming to be 4.0.0-rc.1.
	So this updated to new versions, got the box ready for pascal cards (4 gtx 1080's or 1070's for me) 
	Also I uncomment "WITH_PYTHON_LAYER:= 1 so I can use this option in DIGITS	

I think Nivida is saying they have an web-installer that does better. I don't see how?

I use ModaXterm(Free) on Windows instead of Putty because there was some sort of issue with 
	DIGITS needing an X-Server. 
*************************************************************************
```
#This is written as a script, but I don't see how you could run it as one...
#There is just too many things that change and can go wrong. 
#I just copy and paste one or more lines at a time. 
#But I am just a beginner unix user...

#To further speed up deep learning relevant calculations 
#it is a good idea to set up the cuDNN library.
#For that purpose you will have to get an NVIDIA developer account
#and join the CUDA registered developer program. 
#The last step requires NVIDIA to unlock your account 
#and that might take hours or 1-2 days.
#But you can get started also without cuDNN library. 
#As soon as you have the okay from them – download cuDNN and upload it to your instance.

#Paul's Comment:  If you going through this much trouble, 
#I would just register as a developer and download CuDnn first. 

#FTP Install Notes
#FTP is not required, but I think it's handy. 
#There are all sorts of examples of using vsftpd on AWS, but they all a bit different. 
#This is what works for me, just to get things started. 
#This is just for temporary instance that only I would be using. 

#AWS Security group changes: 
#Make sure 20-21 and 1024-1048 is open to your IP
cd ~
sudo apt-get update
sudo apt-get dist-upgrade
sudo apt-get install vsftpd

sudo vi /etc/vsftpd.conf
#Add the following lines to the bottom of the vsftpd.conf file:
#Change pasv_address to the Public IP of the AWS Instance:
pasv_address=54.157.147.8
pasv_enable=YES
pasv_min_port=1024
pasv_max_port=1048
port_enable=YES
pasv_addr_resolve=YES
write_enable=YES

#For local servers just these lines needed to be enabled:
write_enable=YES
local_umask=022

sudo service vsftpd restart
cd ~

#I put chrome on local machines:
sudo apt-get install libxss1 libappindicator1 libindicator7
wget https://dl.google.com/linux/direct/google-chrome-stable_current_amd64.deb
sudo dpkg -i google-chrome*.deb

#Installing CUDA 8RC
#Installation of required tools
#A menu pops up, and I just tell it to keep the local version:
sudo apt-get install -y gcc g++ gfortran build-essential \
  git wget linux-image-generic libopenblas-dev python-dev \
  python-pip python-nose python-numpy python-scipy
 
#download CUDA 8:
Download cuda-repo-ubuntu1404-8-0-local-ga2_8.0.61-1_amd64.deb from the NVidia site (You have to register)
# install CUDA 8:
sudo dpkg -i cuda-repo-ubuntu1404-8-0-local-ga2_8.0.61-1_amd64.deb
sudo apt-get update
sudo apt-get install cuda

# setting the environment variables so CUDA will be found
echo -e "\nexport PATH=/usr/local/cuda/bin:$PATH" >> .bashrc
echo -e "\nexport LD_LIBRARY_PATH=/usr/local/cuda/lib64" >> .bashrc
 
sudo reboot
 
# installing the samples and checking the GPU
cuda-install-samples-8.0.sh ~/
cd NVIDIA\_CUDA-8.0\_Samples/1\_Utilities/deviceQuery  
make 
./deviceQuery

#At this point deviceQuery should have given you a bunch of information about the GPU(s?) and passed tests. 

# Install CuDNN v6
#You can't just wget the file
#You have to register as a developer and manually download. 
#This is why FTP was the step before this. 
#So first FTP the cudnn-8.0-linux-x64-v6.0.tgz file to home

gzip -d cudnn-8.0-linux-x64-v6.0.tgz
tar xf cudnn-8.0-linux-x64-v6.0.tgz

# copy the library files into CUDA's include and lib folders
sudo cp cuda/include/cudnn.h /usr/local/cuda-8.0/include
sudo cp cuda/lib64/libcudnn* /usr/local/cuda-8.0/lib64

#Installing caffe
#Main source for this and the following step is the readme of the DIGITS project.
sudo apt-get install udo

sudo apt-get install libprotobuf-dev libleveldb-dev \
  libsnappy-dev libopencv-dev libboost-all-dev libhdf5-serial-dev \
  libgflags-dev libgoogle-glog-dev liblmdb-dev protobuf-compiler \
  libatlas-base-dev
 
sudo apt-get install python-dev python-pip python-numpy gfortran

#Install Git:
sudo apt-get install git

# consult https://github.com/NVIDIA/DIGITS/blob/master/README.md
git clone https://github.com/NVIDIA/caffe.git   
 
#This takes a long time,(10-30+ minutes)
cd ~/caffe/python
for req in $(cat requirements.txt); do sudo pip install $req; done
 
cd ~/caffe
cp Makefile.config.example Makefile.config
 
# In Makefile.config uncomment USE_CUDNN :1 
# Also I uncomment "WITH_PYTHON_LAYER:= 1 so I can use this option in digits
vi Makefile.config

make all
make py
make pycaffe   (It says nothing to be done?)
make test
#This runs a large number of Caffe tests:
make runtest

echo -e "\nexport CAFFE_HOME=~/caffe" >> ~/.bashrc
#Load the new environmental variables
bash

Install Torch:
https://github.com/NVIDIA/DIGITS/blob/master/docs/BuildTorch.md

Installing DIGITS
#3/26/17 had to run: 'python get-pip.py'because of "No module named packaging.version"

cd ~
DIGITS_HOME=~/digits
#Using currrent build:
git clone https://github.com/NVIDIA/DIGITS.git $DIGITS_HOME
#I backed up to 4.0 release because an issue with the current build:
#git clone --branch digits-4.0  https://github.com/NVIDIA/DIGITS.git $DIGITS_HOME
git clone --branch digits-5.0  https://github.com/NVIDIA/DIGITS.git $DIGITS_HOME

#If you don't want the master this is an example of cloning a branch:
#git clone -b dev/lmdb-inference --single-branch https://github.com/gheinrich/DIGITS.git digits

cd digits
sudo apt-get install graphviz gunicorn

for req in $(cat requirements.txt); do sudo pip install $req; done

####I added this line because the pycaffe module was not being found in Digits:
####OK, I took this out and added:  make pycaffe above
####echo 'export PYTHONPATH=/home/ubuntu/caffe/python' >> ~/.bashrc 
####bash 

cd ~

# You might want to consider locating your job-directory ( jobs_dir) on an EBS 
# See https://github.com/NVIDIA/DIGITS/blob/master/docs/GettingStarted.md for details. 
# I set the the jobs_dir at /data/digits/jobs by using the --config option:
#./digits/digits-devserver --config

# start the server
./digits/digits-devserver

#To use opencv in python scripts:
sudo apt-get install python-opencv

#AWS Security group changes: 
#Make sure port 5000 is open to your IP

#To view DIGITS go to port 5000 the public IP of your instance:
#Example:  I pasted 50.16.43.125:5000 in my browser. 

#Mounting a new EBS Volume
#WARNING! Only format a new volume:
#sudo mkfs -t ext4 xvdf
#Create a mount point:
#sudo mkdir /data
#Mount the new volume
#sudo mount /dev/xvdf /data
#Add permissions:
#sudo chmod 777 /data
```

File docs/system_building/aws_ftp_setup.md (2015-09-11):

FTP Install Notes
There are all sorts of examples of using vsftpd on AWS, but they all a bit different. This is what works for me, just to get things started. This is for a temporary instance that only I would be using. 

Security group changes: 
Make sure 20-21 and 1024-1048 is open to your IP
```
sudo apt-get update
sudo apt-get install vsftpd

sudo vi /etc/vsftpd.conf
Add the following lines to the bottom of the vsftpd.conf file:
#Change pasv_address to the Public IP of the AWS Instance:
pasv_address=50.16.43.125
pasv_enable=YES
pasv_min_port=1024
pasv_max_port=1048
port_enable=YES
pasv_addr_resolve=YES
write_enable=YES

#Change password:
sudo passwd ubuntu

#Restart server for changes to take effect:
sudo service vsftpd restart
```

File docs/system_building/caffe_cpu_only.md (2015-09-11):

```
#This is handy, you can rebuild caffe to run it in CPU only mode.
#This works great for classifying or training small networks such as LeNet
cd ~/caffe 
vi Makefile.config
change to:
#USE_CUDNN := 1
CPU_ONLY := 1

make clean
make all -j8
sudo make py
```

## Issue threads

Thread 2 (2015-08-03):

Change DIGITS classify_one call to use .NET instead of call curl.exe

pkrush, 2015-08-03:
.NET currently calls curl.exe. Duct tape...

Help!

I gave up after 4-5 hours trying to post the job_id and image to the DIGITS Rest API in various ways in .NET. I am a bit embarresed about it.

I could not see the error description /models/images/classification/classify_one was sending or something...

I guess I should have looked on the Flask server side or used a packet sniffer or something.

$ curl localhost:5000/models/images/classification/classify_one.json
{
  "error": {
    "description": "The method is not allowed for the requested URL.",
    "message": "405: Method Not Allowed",
    "type": "MethodNotAllowed"
  }
}

$ curl localhost:5000/models/images/classification/classify_one.json -XPOST
{
  "error": {
    "description": "job_id is a required field",
    "message": "400: Bad Request",
    "type": "BadRequest"
  }
}

$ curl localhost:5000/models/images/classification/classify_one.json -XPOST -F job_id=20150518-115153-4047
{
  "error": {
    "description": "must provide image_url or image_file",
    "message": "400: Bad Request",
    "type": "BadRequest"
  }
}

Closed 2015-08-18.

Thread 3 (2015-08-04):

Add Hardware Documentation

pkrush, 2015-08-04:
Add Basic Hardware Documentation for conveyors and belts:
Build Instructions
Bill of Materials
Cad Files

Closed 2015-08-24.

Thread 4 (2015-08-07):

Change DIGITS call to use smaller images.

pkrush, 2015-08-07:
The system is taking around a second per coin. This is about the slowest my SUKO MKII coin hopper can go. (You can just lower the input voltage on the hopper if it's DC to do this.)

I have been working with 256x256 images.
I tried LeNet with 40,000 plus 28x28 images with great success and surprise.
So I need to try 64x64.

pkrush, 2015-08-07:
One issue: LeNet needs to be trained with the same exact type of images and AlexNet does not. The cropped images where just a little different switching from the EOS photos to EOS Liveview, a different focal length, and object distance. Not much of a change to the naked eye in the cropped image. The Liveview images have a different starting resolution and a different algorithm to make them round.

pkrush, 2015-09-09:
I am not so sure about the above comment. It does not matter regardless.

I have learned a lot more about how to change network sizes.

Closed 2015-09-09.

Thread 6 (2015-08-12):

Languages need to be pinned down for the next milestone.

pkrush, 2015-08-12:
I have been following the oft stated advice for involved CV projects that:
        “You’re better off getting whatever you need to do working first on the PC in C++ then moving it to mobile.”
In addition to:
	“It’s 10 times easier to prototype in MATLAB and port to C++, then to just use C++ alone.

I would love to hear from others it’s this still applies…
Is Python coming of age that you can use it for both prototyping & production?

Planned Platforms:
Hosts: Windows, Linux, Android
Server: Ubuntu

System language direction:
To have little or no code in a proprietary language
Remove VB.NET in favor of C#
C++ for image processing
It’s hard with so many platform combinations.

First Prototype:
GUI: VB.Net
Preprocessing (crop, basic object detection to reduce server load): Matlab
Image Processing: Matlab
Server: Caffe/Digits (Flask/Python) but no custom software or scrips.
Camera Control: C#
Host side Hardware control: VB.net
Hardware: HP, but no custom software

Future Windows Prototyping:
I don’t know. Matlab/Octave & Python?

Production:
GUI: Command line, Windows C#, Java Android.
Image Processing: Maybe none on the host, or C++ for preprocessing.
Server: Caffe/Digits (Flask/Python) Custom Caffe control will be Python. C++ for image processing.
Camera Control: C#, Java
Host side Hardware control: C++
Hardware: Arduino or maybe Raspberry PI

Labeling:
Flask/Python

Server side GUI:
Nice because it would be the same across platforms.
So starting the conveyor requires internet access?
Why not? If the system needs internet access to classify.

I don’t know if I need to do image processing. It might be fine to crops images and send them directly to Caffe.
I don’t know where and when classification will be done.

pkrush, 2015-09-09:
After using Caffe for a while I can see there is plenty of power in a CPU to classify.
The next few milestones are Windows based classification tools.
So it's C++ for the back end, and C# for the GUI.

Closed 2015-09-09.

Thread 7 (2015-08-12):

Add Windows support for web cams

pkrush, 2015-08-12:
With enough light I got a pretty sharp image off a cheap web cam with the belt moving at about 100 mm a second. Something like a 640x480 picture of a 13x10mm section of the penny. I'm impressed, I did not think you could do that without it being blurred.

pkrush, 2015-09-10:
In doing this I also need to add guides for much tighter physical vertical control of the coins.

pkrush, 2015-09-29:
I wrote the first real time classify and rotate with a webcam code.
It's ugly and the network can be way better, but it does work!

pkrush, 2015-09-30:
Done.
I am using one of these 50-500x microscope cameras. It works but needs more light to take clear pics when the belt is moving. Maybe 20x would be better so it can be closer. It's 8" away.

Closed 2015-09-30.

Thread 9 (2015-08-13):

Add automatic camera calibration & motion skew function

pkrush, 2015-08-13:
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

The current script is not set up to handle different cameras, lenses, belt speeds, or even camera positions.

It would be nice to have a way to automatically get images of round coins.

The neural network has no issues with deformed looking coins, but round coins are nice for human viewing.

Round coins might (I don’t know) be needed for determining rotation.

I tried, but the MATLAB camera calibration does not account for the skew that is created because the belt is moving and the camera sensor is only sampling one line of the image at a time. The image is sharp, but a round coin becomes more oval the fast the belt is moving.

---

I am thinking one easy way to do this is determine the corners on a checker board covering most of the viewing area and remapping the image with something like MATLAB's imtransform.

I guess the right way to do it would be deskew, do camera calibration, then adjust the image for homography because the camera will never be square. I am guessing all this is unnecessary if you have a constant viewing plan.

pkrush, 2015-09-10:
The image plane or belt speed is not going to change. Therefore I don't think you need to use camera calibration and de-skewing. You just need to read the checkerboard and do a transform to make it correct.

No MATLAB, this needs to be in OpenCV.

Determining rotation does work great with round coins.

pkrush, 2015-10-03:
I put in a de-skewing function for the current belt speed, but an automatic calibration function is just not needed for the 2nd Proof of Concept milestone.

pkrush, 2016-02-11:
On the hardware side I should try pulsing LED’s:
To get motor RPMs.
To get belt speed
I need to hook up the LEDs anyway.

Closed 2017-12-06.

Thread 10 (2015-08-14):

Improve the cropped file name Layout

pkrush, 2015-08-14:
Cropped File Name Layout:
Len  Example Desc
3	106         Run Number
6	100001   Image number
1	1             Belt number (This is if there are more than one belt in the image)
2	01           Crop Number (Say 10,11,12,13 when there are 4 pennies in the image)
4 	1025       Coin center in pixels from edge.

Example
1061000011011025.jpg

It seems like you should code some of this into file folder naming, but you need to mix image files from different runs.

You could have a key and look this up in a database, but this is simpler.

It would be better to store images in a database. And LMDB looks like it’s the way to do, but it has to wait to a Python port.

I am guessing that in production a system is not going to use a perfectly cropped undistorted images for training and classification. But they are nice for people to look at and will be able to cross over to systems that have different cameras, lenses, lighting, belt speeds, backgrounds, Etc.

Closed 2015-08-16.

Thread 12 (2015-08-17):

Build local server & document design

pkrush, 2015-08-17:
A LInux machine to function as both a server and later a client machine driving the process with a web cam.
Software wise it should be almost the same build the as the AWS build.
It will be built around a GTX 970 GPU only because I have it already.

1.) Spec out what it needs to be.
2.) See what the AWS machines use resource wise.
3.) Order parts
4.) Build the hardware
5.) Script the software build

After this server build we need to look at a:
1.) Caffe ported to Windows
2.) A minimum Linux box (I am betting you can build something that is 4 times as fast as a TK1 for only a little more money) GT 640's?
3.) A Jetson TK1 or a TX1 if it's out yet.

It's hard to spec something out without know the use case!

pkrush, 2015-09-10:
The plan is now for users to classify with Windows Only.
DIGITS does not work on Windows or the Jetson TK1(it's an ARM).
So a local server is wanted only for training using DIGITS.
Why not AWS? A local server will save time, hassle, and cost less. Somewhere pennies an hour for machines turned into almost $100 already and I am only getting started.

This is a want, not a need. I could train using the Windows Caffe port, but I think in the end DIGITS will save me enough time to make it worth it.

pkrush, 2015-09-17:
I got parts for server on the smaller side just for training.
Intel G3258 Processor(Smaller), 8GB of Ram, 250GB SSD, MSI H81M-E33 motherboard. $280. Let’s see how it’s works with the GTX 970 for training…

pkrush, 2015-09-22:
I built the server and got DIGITS up. Yea!

Closed 2015-09-17.

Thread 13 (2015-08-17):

Create Android App to Sort

pkrush, 2015-08-17:
Basically replicate what is being done on the PC in Android.

Currently a Windows PC classifies Caffe models and sends commands to control Arduino based conveyors and solenoids for sorting coins. An Android based system would great option to reduce the cost, size and complexity of the system.

Skills Needed:
Android, Arduino, OpenCV, C++, Python, SQL, image processing, machine learning, Caffe, convolutional neural networks

pkrush, 2015-09-09:
Heck it would be cool to make a no hardware coin finder. It would just high light coins on the screen.

pkrush, 2016-02-05:
Just an app to prove how quickly a device processes the images is a great first step. Building out a system to fully work on Android might not be worth it until the system is out in the wild on the PC side.

Closed 2017-12-06.

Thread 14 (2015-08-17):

Port Matlab Code

pkrush, 2015-08-17:
MATLAB Code needs to be removed to simply and “open” the system.
What is being done in Matlab is pretty light weight:
It finds the penny outline to crop it
It finds centers of pennies to tell the solenoid when to turn on.
It rounds the pennies because lens and moving belt.
It crops images

pkrush, 2015-09-10:
This is covered by other issues.

Closed 2015-09-10.

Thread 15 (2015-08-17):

Try classifying by windowing uncropped images

pkrush, 2015-08-17:
This dumps the Matlab code and makes it possible to classify pennies that are cut off.
There is plenty of detail in an image of a coin that is a little warped and 50% cut off to classify it.
You don’t need one pixel center location accuracy for the coin
Make the coin path 256 wide?
Send the 256 x 960 crop to digits.
Window over the crop.
Also at this point I don’t the best image height. I suspect it’s less then then 256 and maybe a lot less. It depends on what you are after.

pkrush, 2015-09-10:
Image resolution depends on what you are after. 256 is needed for date capture. I think more then 256 is needed to determine S vs D mint marks.

I really don't think directly classifying is the way to do.

**This is the current plan:**
1.)	Capture the image
2.)	Transform the capture to remove lens distortion and belt skew (Round coin)
3.)	Find the coins
4.)	Find the center of the coins
5.)	Crop the coin image

Closed 2015-09-10.

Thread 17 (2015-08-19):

Come up with a better coin switching mechanism

pkrush, 2015-08-19:
A solenoid certainly seems the most logical.

Such as low cost push solenoids to knock/hammer coins off the belt:
Maybe some type of foot it's more then just the rod end, but try without a foot first.

Rotary solenoids seem like a good idea, but I have not seen many.

If you position you could sort to more than one bin:
RC servos since they are so common and easy to control.
Cheap stepper motors might not be a bad idea. A step past a rotary solenoid.

pkrush, 2015-09-10:
Solenoids have a short travel so it might be better to switch on the thickness of the coin. Also they pull in. So a solenoid closer to the hinge with 2.5mm travel can drop a slide say 6 mm down on the end. I have to post a drawing.

pkrush, 2015-11-13:
Lets change this to:
Come up with a new coin switching mechanism, and do it in less then an hour, and don't care if it works...

pkrush, 2015-11-19:
A friend mentioned air which would go great with all sorts of other small parts as well. I tried it, it does work with little air, but it does require a compressor.

pkrush, 2015-11-19:
I tried just a push pull solenoid. One that has the plunger coming out of the back so it can push when powered. It's pretty cool. You can shoot the penny like a billiard ball and cause it to fly off in different directions. This is cool! If I have good timing I can use one solenoid to fill 3 different buckets.

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

pkrush, 2015-11-19:
This is fun. So the next task is to make an pinball game with pennies.

pkrush, 2015-11-20:
If you used PWM you could also vary the power to hit different buckets.
But not if your using a relay. I need to test with a relay. Also a looping test track would be nice to try to wear such a system out. I worry the plunger will mushroom over.

pkrush, 2015-11-23:
Applying billiard ball English with the solenoid end just works to hit 3 bins with one solenoid.
I tested this with three push solenoid settings:
-50ms
Zero (coin center)
+50ms
The belt is running at 72mm per sec. So this works out to hitting the 19mm penny 3.6mm off center. It’s pretty consistent and there is room for the timing to be a little off.  The end of the solenoid is a flat rod. (It’s threaded M3-0.5)
I am thinking you can hit the coins into PVC pipes built into the frame and put bags under the pipes. Also at least for test I would like IR sensors in the pipes to prove the system is working correctly.

Also the solenoid is strong enough to so this with half dollar coins (11.3g 30.5mm). This is largest common US coin.

pkrush, 2015-12-16:
**So design and make it:**
3 way solenoid sorter:
Uses cue ball English and a push solenoid to pop coins into one of three PVC pipes.
Sequentially sorts all the pennies so none should fall off the end of the belt.
Put in IR sensors to test if the system is sorting correctly.

pkrush, 2015-12-22:
Some bins will be smaller some bigger. Try using 1 liter pop or water bottles as they are cheaper and more common then PVC Pipes!

pkrush, 2016-01-12:
I build one test conveyer with a solenoid...

Test the English on this one:
Make and install the new top plate.
Mount the IR sensor and LED, solder and heat shrink.
Solder 2 motors with flexible wires.
Test the English
Can I detect stacked coins?

Revisions needed:
Make the conveyor longer to have the 3 buckets
Redesign the top plate
Move the solenoid away from the motor.
Solenoid plate should have locator tabs
I wonder if the nuts should be different heights so all the screw lengths are the same?
Use all 3mm screws?
Somehow I cut 3mm end plates mirrored, be careful next time.
Clearance holes in the side rail to tighten the solenoid plate?
The motor axis can be moved 1mm down in Y.
Clearance for a light strip
Bigger holes for bushings.
Lift side rails above the ir sensor 0.5mm
Can the end plate be any wider to square the side rails more?
Keep the old conveyor together.
Build a new conveyor and start building the assembly instructions at the same time.

Start of assembly tips & instructions:
Cut coupling tubing 17mm
Cut 30mm wide belt 7 ½ inches long, bond smooth side in. Tape before heat sealing.
Mirror the side rail when cutting.
Don’t tighten top plate super tight as it will crown.
Cut 2mm shaft 41mm long
Cut 2mm shaft 57mm long
Drill out bushing holes with a #13 drill
Squeeze the side rails when screwing on the end plates.

pkrush, 2016-01-13:
I call this done with the solenoid pictured above knocking coins into 2 different boxes. It will incorporated into the scanning conveyor.

pkrush, 2016-01-19:
I used an IR sensor and one solenoid to push the coin into 3 different bins. This is useful, but complex. If I use one bin per solenoid and have a wide foot the tolerance will go up 10x. I can add a wide foot to the solenoid since it’s pushing into a 4” wide box. Instead of needing to get into a 3mm window it can be a 30mm window! I don’t need that many bins at first, so using one solenoid per bin will be much easier to start out with.

Why are IR sensors bad? Both the LED and sensor have a resistor, this is a lot of wiring. They could get dirty. There is code and tuning involved.

Closed 2016-01-13.

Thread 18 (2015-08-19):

Meter coins with a DIY conveyor hopper instead of a stock coin hopper

pkrush, 2015-08-19:
This is important for a number of reasons:
1.)	It greatly lowers the cost of the system
2.)	Coin hoppers are loud! A conveyor hopper
3.)	Coin hoppers are range limited for coin diameter and thickness. Building a multi-conveyor hopper will allow the system to sort mixed coins (loose change).
4.)	It greatly expands use of the system beyond just one size of coin, and to all small parts in general, such as:
* Parts: metal, plastic, glass, wood, pellets, electronic components, ball bearings
* Fasteners: screws, nuts, bolts, washers, spacers, pins, buttons
* Ammo: bullets, fired brass casings, primers
* Scrap: Small, Shredded, or broken, metal, electronic waste, glass, plastic
* Craft: Pebbles, gems, stones, beads, mosaic tiles, mine concentrate
* Pharmaceutical: capsules, tablets, pills
* Food: seeds, beans, grain, dry fruit, Fruit Loops, candy, Jelly Bellies
* Small toys: Legos, blocks & tiny connector toys, puzzle pieces

For coins this not a hard task to design. You need:
* The right conveyor speeds
* Conveyor combinations.
* Fingers on the sides and top getting coins in a single file line.
* Maybe abruptly stopping or reversing the belt.
* Maybe vibration in places.
* Maybe vibratory slides.
* You need to handle the possibility that coins are stacked or stuck.

I think this could be just as, if not more, long lasting then a purchased coin hopper.

I think a kit would have a number of stock fingers and parts to help with metering any parts.

pkrush, 2015-12-16:
**Semi-auto DIY Hopper area:**
An area/open container that the coins can be poured into.
It should hold 1-3 liters of pennies.
Maybe at some point above can be a 5 gallon buck with a 3” hole in it that coins would flow out of.
The input belt would pull the coins from out of this.

**Off the self vs DIY hopper vs hand feeding:**
This is very low cost replacement for hand feeding the belt and not meant to be an unattended high volume system. Still I think this can be tweaked to feed a huge number of coins an hour, say 10000 plus. This is 60 plus pounds an hour; A level that requires occasional handcart usage!

pkrush, 2016-01-13:
This is the same as the input conveyer.

Closed 2016-01-13.

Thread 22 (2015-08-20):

Don’t save empty image captures

pkrush, 2015-08-20:
Change MATLAB script to delete images that have no big blobs. Or save just crops of images with pennies. This would be better for the published dataset.

pkrush, 2015-09-10:
I think a better goal is don’t save image captures at all. Don't go to disk with files at all.

Closed 2015-09-10.

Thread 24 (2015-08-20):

Show real time counters & statistics as the system is sorting

pkrush, 2015-08-20:
**Show real time counters & statistics as system is sorting**
- Mostly for improving accuracy at this point
- All Imaged
- Types of coins found
- Coins missed by the camera, but caught by an IR sensor
- Average milliseconds for different parts of the process
- Coins per second

This also would be great for turning off the system if it ran out of coins or stopped working for some reason.

Closed 2017-12-06.

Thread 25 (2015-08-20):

Add more sensors to the system

pkrush, 2015-08-20:
**The two that make the most sense:**
- Electromagnetic sensor to signature of the eddy currents. Like the kind in a coin discriminator,
  but you can do why more with the data by bring it into a neural network!
- Line camera (cheaper, faster, but less DIY)

**I’m sure someone will work with:**
- Coin rolling acceleration (I did a few years ago, it does correlate with coin/metal type.)
- A microphone
- Other light spectrums

I really hope this project has enough interest to demonstrate adding an XRF module to the system to exactly determine metal elements present. Please contact me if you have one I can borrow or you’re a XRF manufacturer and you wish to demonstrate you products. I know people would love to see this for coins, but I really want to try sorting small zorba metal scrap and shredded e-waste. Zorba is mostly from shredded cards and it too has coins!

Closed 2017-12-06.

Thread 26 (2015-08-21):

Capture both sides of the coin at once

pkrush, 2015-08-21:
Ideas:

Two Cameras, top and bottom or one camera on top with an angled mirror. They you could use a clear belt (or slide), or some transport with a gap / hole(s). Maybe two belts (or slides) on each side with a gap in the middle. If you don’t need the whole image a slide with holes might perfect.

I’m sure there would be a ton of pros and cons with clear belting. I have lots of clear Polyurethane .3x30mm belting.

One camera: The coin passed on a belt, flipped off the end of the conveyor on to a conveyor heading in the opposite direction and back up to be imaged again by the same camera. I have done this. There is timing issues and I did not try to correlate both sides of the coin.

A very compact low cost way is two line cameras on each side and do a helical scan as the coin rolls by! I have to learn more about this…

My favorite right now is to **catch it in mid-air with two cameras** top and bottom as it’s jumping from one belt to the next. It takes a lot of light to do this, but I am pretty sure you could do it with cheap $5 web cams.  I still can’t believe they can handle this kind of speed and the image stays sharp.

A similar method would be dropping if off the end of a belt or slide and capturing it from both sides. Kind of like how they sort falling materials with puffs of air.

pkrush, 2015-09-10:
A clear belt and webcams top and bottom it is.
I don't know if clear belting will stand the test of time, but it will work find for testing.

pkrush, 2016-08-30:
A clear belt sticks too much.

Closed 2016-08-30.

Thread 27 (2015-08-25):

Future Milestones

pkrush, 2015-08-25:
There is clear demand for a coin sorting and inspection tool, but it’s not just people interested in coins that would use this.  Since everyone one understands what coins are, coins a great "small part" to demonstrate what a low cost system like this can do. It's also a great project to help people learn computer vision.

**Beyond coins, the overall goal is a open low cost system / kit that can:**
- handle, image, inspect, count, sort, and position small parts.
- with local or remote control.

With such a system users would train the network for their own parts.

pkrush, 2015-09-25:
After the Proof of Concept 2 milestone this is a logical next step:
1.)	Test using the software on various Windows boxes and laptops.

I am going to need help with this one. I think a Vision Maker Meetup at Workshop88 is in order for this.

pkrush, 2015-09-28:
Coins have always been the first part of many. Sorting is the first task of many. I can see that this project will evolve quickly beyond coin sorting. Quicker than I thought it would.

I love working with small parts for at ton of reasons(another list for another day).

**Other parts to work with:**
* Parts: metal, plastic, glass, wood, pellets, electronic components, ball bearings
* Fasteners: screws, nuts, bolts, washers, spacers, pins, buttons
* Ammo: bullets, fired brass casings, primers
* Scrap: Small, Shredded, or broken, metal, electronic waste, glass, plastic
* Craft: Pebbles, gems, stones, beads, mosaic tiles, mine concentrate
* Pharmaceutical: capsules, tablets, pills
* Food: seeds, beans, grain, dry fruit, Fruit Loops, candy, Jelly Bellies
* Small toys: Legos, blocks & tiny connector toys, puzzle pieces

pkrush, 2015-09-28:
I am digging through my screw bin for 10-24 screws right now. If trained could Caffe find 10-24 screws that are among 10-32 and 8-32 screws. Of course!

pkrush, 2015-10-02:
Detecting Arrowheads with drones & computer vision

It’s getting way easier to find stuff with computer software. For example you can train a program to understand the difference between a rock and an arrowhead in an image from a camera. I still think a human would be better unless camera was able to travel more ground, or “ground” was moving past the camera on a conveyor belt. Drones are really cool, but I have a feeling setting up lines for the camera to travel cable car style would be the way to go. Open ground and lots of light would be best.

Of course one could look for whatever they can see with their eyes: minerals, gems, fossils, and other relics. There would be an advantage in looking for tiny stuff. It’s easier to make the camera cover more ground and it could see small things much quicker than your eyes can.

What do you think? Do you see this happening? I do, it’s not half baked sci-fi. It wouldn’t be perfect, but it would speed up the hunt. I would love to build the equipment to do this. I am working with coins right now, but this tech (deep learning) is easy to adapt.

Out of curiosity what sorts of things would you look for? What area do you think people would be the most interested? Scanning for their lost keys?

Thanks!

Paul Krush
GemHunt.com

pkrush, 2015-10-02:
Detect the same coin twice:

Yes! One could make [Where’s George](http://www.wheresgeorge.com) for coins.

I see this as a useful feature. People are going to look back at images from previous batches and really want a single coin. It would be a lot easier to do this then to look through a 5 gallon bucket it when into.

This would be cool for inventory systems as well. Virtual coin picking systems. Scan the junk bin and post it on a website. Then shipment time comes and the system can fine the same coin to ship out.

Before I tried deep learning I tried classical feature detectors such as SIFT. They could find the same coin, but had a lot of trouble finding the same design on a different coin. My bet is at a deep enough level of detail the nicks and wear on a coin is like a finger print positively ID coins twice. And what if you started finding worn coins with the same exact details? Counterfeits!

pkrush, 2015-11-12:
My current plans are to keep working on this coin sorting project till fall 2016. It’s based on the low end coin market. Finding & discovering new verities and errors. Low end grading. Low end auto rotate hobby inspection. Mass Coin Imaging. It’s all kind of related and the tools are the same. If the demand is there I want to try metal content detection with eddy currents, trained with XRF.

pkrush, 2015-11-23:
Pump live sorting video to Twitch. There are all sorts of image updates you could do. Live feed of the system. Live head shot. "CNN/ESPN" style feed of latest finds.
OK, this is way out there, but would make for a great chat room.

pkrush, 2015-12-12:
It would be really nice if there was a way to automatically test camera setup performance. How the system performs as a whole(camera, lighting, focus,etc).

pkrush, 2016-01-13:
Make a many bin sorting conveyor on a 72” x 30” table

I don’t know how people would really want to do this, but it can be done for pretty cheap.

Out of curiosity I did a mock up where one solenoid knocks a coin into ether 2 boxes or chutes. The chutes could go to bags in the floor.

You could go nuts with this. One could use more levels and smaller boxes. For a demo I think clear boxes would be neat.

The boxes would be 4”x4”x8” boxes cut in half on a small angle. You can buy this for about 30 cents each, but they happen to be the same size as penny boxes.

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

pkrush, 2016-01-13:
OK so that post above would be more interesting if each bin was a person.
A high speed in person low value coin trading system
or
call it the junk bin swapping system
See [SortNSort.com](SortNSort.com).
Say you have 8 people around a 60" round table and conveyors shuttle coins to and from each person. The conveyors would be under glass so the table would be mostly usable.
I though of this years ago. One computer can control it with displays mounted in the middle and above the table so people could still see each other. Each person could get a $1 keypad. A low cost system.
Of course today it could just be smart phone based...
For more fun this could incorpate gambling. Not just coins could be moved. Cards, poker chips, gem bags, anything small.

pkrush, 2016-08-25:
Label the facts of wear and the general grade? It would be nice to label coins down to yes/no questions. It would be nice to see how the labels and the grade correlate.

Closed 2017-12-06.

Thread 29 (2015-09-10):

Make CoinSorter more accessible to other developers

pkrush, 2015-09-10:
**This is a meta-issue, but it’s worth posting anyway:**
* Drop MATLAB, use OpenCV
* Drop HP Control, use Arduino
* Drop AWS, use Windows Caffe build
* Drop Canon EOS (Rebel Camera), use a webcam
* Drop VB use C# (Not more open, C# is gaining on GitHub)

**Compiling Caffe for Windows is a lot of work:**
* Find or build a stripped version for just classification
* This should available as a binary

*******What is this missing in this 2nd Proof of concept milestone******************
Great documentation
Production error checking
Production friendly design.
No research in what else can be done.
No web based labeling or remote control
Software only designed for pennies.
No Android or Linux version
Not for CNN training
Bloated Caffe classification caffe core.
Trusted Microsoft Windows Store Install
	For security reasons I don’t think it’s no longer safe to offer compiled binaries production release.
Fortunately this looks much more possible than years past
In the past there were USB Control, OpenCV, Win32 issues

pkrush, 2015-09-25:
Why C#.Net 4.0 for the GUI? The goal is to get something done soon! This can be changed. It’s just the GUI, the backend stuff is going into C++. Qt or web would slow things down way too much. Mobile does not have the power. At this point Window 7+ boxes are like 80+% of what is out there. When the system is running and people want it we can think about other OS’s and devices. Also building it as Windows Store app is needed in the future.

pkrush, 2015-10-30:
Done. This sure slowed me down, but now others can use this. Almost.

Closed 2015-10-30.

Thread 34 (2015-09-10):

Find coin centers

pkrush, 2015-09-10:
Currently this is done in MATLAB. This function needs to be moved to OpenCV or part of the Caffe classification.

pkrush, 2015-10-03:
The MATLAB version was not that good it skipped coins.

So far I have used an IR sensor below the belt and an IR LED above the belt to get the ground truth to test the software.

I used findContours in openCV but it's not as good yet.

I need to change the guides tighten up the path of the coins on the belt so the vertical variance is less.

This needs to handle the case of the coins touching. I am thinking it might be better to look for coin segments on top and bottom. Maybe do a little math that confirms this is a coin segment.

pkrush, 2015-10-03:
Move the guides to the get the coin path tight
Put IR sensors on both top and bottom and read them from an Arduino
Get this data into C# via serial
Then put it in a SQLite database
Correlate this data to make sure the two sensors correlate to each other.

pkrush, 2015-10-22:
Done
This is harder with the webcam images because the color washed out at the higher light levels needed to stop blurring. I had to use the Cb channel in YCrCb to tease out the penny from the belt. This will not work with a more dirty belt and a silver colored coin.

Closed 2015-10-22.

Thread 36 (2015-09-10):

Power the solenoid with an Arduino

pkrush, 2015-09-10:
Just a swap for the HP Power supply for now.
I don't think this will to hard...

I am waiting for UNO R3 MEGA328P boards and L293D shields to come from China.

pkrush, 2015-09-22:
I got the boards yesterday. This looks like it will be a piece of cake.

Closed 2015-10-15.

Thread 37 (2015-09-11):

Input conveyor

pkrush, 2015-09-11:
The conveyors work great for in house testing. This is about getting them into people’s hands for testing.
All new laser cut, 3D printed, or sourced parts

They need to be easy to make and work with a single frame setup.

Put bearings in them? They are really cheap and might allow for lower cost motors, but I am not sure about this. I really just want to test the system out in the wild before making too many improvements.

Test running on the 1/4” shaft coming off the motor with just tape for a pulley.

I bet I could make an all laser conveyor and zip tie, or even glue the bearings in. I can see 1/8 or ¼ wood pinned.

The gears motors are highest cost part in the system. They conveyors could be designed with DC motors and run straight with no gear reduction, or have an even smaller motor with a single belt reduction. I don’t think this is worth doing at this point.

This issue is really the same as [The hopper Issue](https://github.com/GemHunt/CoinSorter/issues/18).

pkrush, 2015-12-16:
**Input conveyor to pull coins up from hopper area:**
A conveyor on an angle to allow the doubled coins to slide off
Only 19.2mm wide to stop larger coins from traveling up the conveyor.
Not a multi coin sorter. Larger coins can just be picked off by hand.

pkrush, 2016-01-07:
I’m really happy with the first laser cut direct drive (non-gear) conveyor build. Very low cost, easy to build, powerful, and quiet. It’s like $2-4 for parts!

Time redesign the conveyor again:
Cut shaft on last builds.
Start saving the conveyors on wall.
Design for the new 3/16 spacers
Go back to a 30mm belt thin frosted.
Make the more bearing hole for the 280 motors.
Make it easier to put the belt on.
The top has to be acrylic because of the 2mm, and the coins could be backlighted.
Drill out the bore holes as they are not square and tapered
Push motor plate in so there is more drop off clearance
Round some corners
Cut the middle side rail mirrored so the two counteract each other, also cut it so the clean side faces out.

Changes To Add Solenoid:
Top Plate has to be notched for the solenoid rod.
Draw the solenoid.
Solenoid plate is 6mm screwed into the side rail. Mount it so it wants to angle up.
15mm hole spacing
7mm from end
Mounting plate needs to be around 7.5mm lower than conveyor.

pkrush, 2016-01-13:
That worked awesome.
Not sure there is much a different between the input and spacing coveyor. I need to build the others first and work back to this one.

pkrush, 2016-02-03:
This is done. It needs to be used in the system and documented

Closed 2016-02-03.

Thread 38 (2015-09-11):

Portable Prototype Coin Sorter New Issues

pkrush, 2015-09-11:
I think it's a bit of issue pollution if I start posting every issue for this milestone because the "2nd Proof of Concept" needs to be finished first.
- Study, stand-alone frame that holds everything. Electronics all mounted with mounted power strip. 2+ redesigned solenoids leading to 3+ bins
- Get PWM for conveyor motors running.
- IR sensors for post solenoid detection
- Rough bill of materials with sources. (Order parts)
- Do a complete new build at least once for documentation & video.
- A no CPU mode:  Sort by coin size, metering, color.

pkrush, 2015-10-01:
A compact system will need better lighting. The more light you can pour on the coins, the quicker the belt can move, even with the cheapest of webcams. They have these little ring lights that are only 32mm in diameter. Each light is individually addressable. I have not needed it but this might be able map the 3D surface of the coin by running the light around the coin. The highlights and shadows would change for areas with different heights, but not for flat areas.

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

http://www.aliexpress.com/item-img/High-Quality-New-Arrival-8-Bits-LED-Ring-16-x-WS2812-5050-RGB-LED-with-Integrated/32456801618.html

pkrush, 2015-10-16:
Camera Stand for microscope webcam: Adjust in X,Y,Z:
Slots in mount for X and Y.
Z? One screw would be awesome, but I don’t think it’s worth it until I prove this is the best camera.

**50-500X microscope webcam:**
* Is too far away.
* The focus is too course.

pkrush, 2015-12-17:
Just break these out into seperate issues.

Closed 2017-12-06.

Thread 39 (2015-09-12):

Lower cost, all slide, no conveyor, and no hopper version?

pkrush, 2015-09-12:
I am really trying to lower the cost and complexity of this system. I want to be more of a personal system that one can use over and over to discover new features in their coins. Accessibility is more important than speed. Even with hand feeding a slide the system will be really fast.

The hopper has to go, it’s too expensive. This adds complexity.
Then the gear motors would be the most expensive part.

I have played around with this before:
The system could reject coins that are stacked.
It might need vibrators, but these are cheap. I would like to try without them first as I don’t want to add noise.
If the coins need to be slowed down you can reduce the drop angle and use adhesive backed Teflon film strips. This slows them while maintaining a consistent speed.

A great feature of this set up is people can add a hopper if they wanted to.

I think I need to get the solenoid gates working first.

Closed 2017-12-06.

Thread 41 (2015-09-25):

Add a no conveyor webcam & Arduino testing mode

pkrush, 2015-09-25:
This will be great for making sure people can use the software with Caffe as a Windows DLL and the hardware is working. It will give users some confidence before they order anything to build the system.

So this will be the first compiled binaries / software download I put out on GemHunt.com
I should be able to get this out there by the middle of October.

**No conveyor webcam & Arduino testing mode:**
* Webcam mounted down at the table focused with the coin centered and sized at about 80% of the screen.
* Coin can be on white paper.
* In a webcam live view there would be a thin circle where the coin should be.
* In a second live view the image would update in real time rotated correctly.
* Prediction percentages would display in real time.
* Optional: PIN 13 on the Arduino should turn on when a 1982D is found.

pkrush, 2015-09-29:
I wrote the first real time classify and rotate with a webcam code.
It's ugly and the network can be way better, but it does work!

pkrush, 2015-11-15:
I am not sure this will give much confidence because it's going to take a lot of training to get any webcam/lighting set to work with a neural network. The fake camere mode is a better test.

Closed 2015-11-15.

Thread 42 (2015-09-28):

Automatically correlate coin regions/features by date and mint mark

pkrush, 2015-09-28:
This is really cool that this system is going to be able to do this very soon!

Over the years there have been small changes in the (same)designs of coins. I don’t know that much about it. I am guessing current designs are more cost effective to produce. Maybe they use less die force, I don’t know. And really I don’t want to learn what has changed; I don’t want to be bias in what I am looking for. I want the software to discover this. For example the spacing of “AM” in AMERICA is different on the back of US Lincoln pennies after 1992.

Having a large database of coin images and knowing their date and mint mark one could correlate regions on both sides of the coin. You could make thousand maps of what correlates to what does not. Most of it will be meaningless, but some correlations of regions will be quite interesting.

This is pretty neat in and of itself. What is even more awesome is you can use this to find new transitional varieties of coins. Relatively speaking this is not hard to do. I think it’s a pretty obvious next step after getting dates and mint marks.

Closed 2017-12-06.

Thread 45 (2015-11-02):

Get 1959-1982 pennies physically sorting by date and mintmark

pkrush, 2015-11-02:
In past setups I have already have done this with 1982 pennies. By mint mark I mean if the penny has one or not. It’s really hard to tell D vs S with the current camera setup so I am not going to try that. So this is 45 different variations of coins.
I am not going to spend much time training this, because it might have to be done again with a different camera set up.

pkrush, 2015-11-29:
I moved something and I can't get this USB 50-500x Microscope camera to focus when the belt is moving. So I am done with this camera. It did sort, but it was rather unimpressive!

Closed 2015-11-29.

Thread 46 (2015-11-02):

Study, stand-alone frame that holds everything

pkrush, 2015-11-02:
Right now I have everything screwed to the wall. It's not very portable!

Study, stand-alone frame that holds everything:
* Conveyors
* Lights
* Camera
* Controls
* Etc.

Electronics all mounted with mounted power strip.
2+ redesigned servos/solenoids leading to 3+ bins.

pkrush, 2015-12-16:
With PVC pipes that ½ dollars can go into. Size & spec?

pkrush, 2016-02-03:
Mounted the circuit boards seams like one of the last steps. The frame is done.

Closed 2016-02-03.

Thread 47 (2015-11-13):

Make it easier for other developers to help in the project

pkrush, 2015-11-13:
I have been posting code for over 3 months here and I don’t think this project has ever been complied anywhere other than my workstation. It’s getting to the point that this system is doing something useful.

**Tasks:**
- Remove hardcoded directories, and add a configuration file
- Bring the model configurations into the repository
- Add a fake camera and solenoid so the software can be run without any special hardware
- Put images and models on GemHunt.Com to correspond to the 0.2 release point
- Try to build on a different machine and document this
- Build again on AWS and make a public AMI for this
- Finish BuildInstructions.md
- Make a 0.2 release point
- Add a note to the README; something like this:
  _Please fork me: This system is at the point that you could build the hardware and do this yourself. Most likely you will have to build new models from your camera’s images. Also, there is a test mode that you can use the system without a camera or solenoid controller. You should be to clone or fork release 0.2 and get this system to work with the release 0.2 images and models out on GemHunt.com. It’s rather difficult to compile this, as there is a huge C++ DLL project and a C# project.  Click here for build instructions. Or you cheat: I built this already on AWS and made a Public Windows AMI. Also click here for the Linux Training Server AMI._

pkrush, 2015-11-15:
Rotate.cpp::cropCircle has hard coded Dir

pkrush, 2015-12-09:
Done so far:
* Bring the model configurations into the repository
* Put images and models on GemHunt.Com to correspond to the 0.2 release point
* Make a 0.2 release point

pkrush, 2015-12-09:
**I have change this to an end goal for the prototype milestone:**
* Remove hardcoded directories, and add a configuration file
* Add a fake camera and solenoid so the software can be run without any special hardware
* Put images and models on GemHunt.Com to correspond to the 0.3 release point
* Try to build on a different machine and document this
* Build again on AWS and make a public AMI for this
* Finish BuildInstructions.md
* Make a 0.3 release point
* Add a note to the README; something like this:
*Please fork me: This system is at the point that you could build the hardware and do this yourself. Most likely you will have to build new models from your camera’s images. Also, there is a test mode that you can use the system without a camera or solenoid controller. You should be to clone or fork release 0.3 and get this system to work with the release 0.3 images and models out on GemHunt.com. It’s rather difficult to compile this, as there is a huge C++ DLL project and a C# project.  Click here for build instructions. Or you cheat: I built this already on AWS and made a Public Windows AMI. Also click here for the Linux Training Server AMI.*

Closed 2017-12-06.

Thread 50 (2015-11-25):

Upgrade cameras & Lighting

pkrush, 2015-11-25:
These 50-500 Microscope USB cameras are not the way to go. They are really hard to focus in general and much harder with the belt moving at 72mm a sec.

There is a lot to say about this...

pkrush, 2015-11-28:
I might be too much at $40...
[I ordered one of these:](http://www.aliexpress.com/item/2MP-640X480-MJPEG-120fps-2-8mm-lens-1-2-7-CMOS-OV2710-black-and-white-full/32367848952.html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,searchweb201644_5,searchweb201560_1)

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

pkrush, 2015-11-28:
[ELP](http://www.elpcctv.com/) looks like a great company to get cameras from. They sell on AliExpress, eBay, and Amazon.

pkrush, 2015-11-29:
Here are two more companies that stock low end machine vision cameras. It would be nice to get a camera with global shutter, but I have yet to see one under $50.

www.leopardimaging.com
www.e-consystems.com/

Closed 2017-12-06.

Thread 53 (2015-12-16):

Hardware Proof of Concept End Goal

pkrush, 2015-12-16:
This is a hardware test with Arduino software only.
No Cameras, just IR & photo sensors
This setup is the proof of concept for the prototype coin sorter hardware.
This system should mostly run on its own.
See issues for the details of this system.

**Semi-auto DIY Hopper area:**
An area/open container that the coins can be poured into.
It should hold 1-3 liters of pennies.
Maybe at some point above can be a 5 gallon buck with a 3” hole in it that coins would flow out of.
The input belt would pull the coins from out of this.

**Off the self vs DIY hopper vs hand feeding:**
This is very low cost replacement for hand feeding the belt and not meant to be an unattended high volume system. Still I think this can be tweaked to feed a huge number of coins an hour, say 10000 plus. This is 60 plus pounds an hour; A level that requires occasional handcart usage!

**Input conveyor belt:**
A conveyor on an angle to allow the doubled coins to slide off
Only 19.2mm wide to stop larger coins from traveling up the conveyor.
Not a multi coin sorter. Larger coins can just be picked off by hand.

**Coin Blocker:**
Physically only allow cents to go through and stop stacked coins.
Depending on how the coins are stacked this is going to jam.
Also non-pennies, bent, gunked, glued, gummed, etc coins will get stuck.
Sense current to know when the belt jams
To clear:
Run in reverse
Vibrate by running in both directions
I am think this is enough. It’s going to jam every so often and this is OK, it a low cost semi-auto system. The user can just clear it.
If it’s a huge issue maybe use solenoid to remove coins from belt.

**Slide Accumulator:**
A slide to buffer the varying output from the input feed.
I think the material is an open question. Delran? Acrylic? Waxed wood? Sheet metal?
Even a stock hopper would be benefit from an accumulator.
Put an IR sensor near the top of the slide. If it’s blocked slow or stop the feel belt.

**Why an Accumulator?**
This system has higher throughput when the coins are more uniformly spaced.
For a given camera & lighting setup there is a max speed of the imaging conveyor before the images get blurry.
The camera images the coins better with a slower belt.
A lower cost camera can be used with lower belt speeds.

**Imaging Conveyor:**
Sides only 19.1mm wide to make imaging easer.
Clear belt just to start using it. It will be needed later.

**3 way solenoid sorter:**
Uses cue ball English and a push solenoid to pop coins into one of three PVC pipes.
Sequentially sorts all the pennies so none should fall off the end of the belt.
Put in IR sensors to test if the system is sorting correctly.

**Frame for Coin Sorting Hardware Proof of Concept**
A standalone frame to hold all the parts of the system.
With PVC pipes that ½ dollars can go into. Size & spec?

pkrush, 2016-01-13:
Again what am I trying to achieve?
Still only worry about 3 bins for now.
How good can the feeding and spacing get?
How well do the laser cut conveyors with direct drive motors work? (Really good so far!)
The 3 ways solenoid works, but I am going for a two way to simplify the design.
I need to build a working proof of concept for the solenoid.
How well does the camera under the belt mount? I am not trying to use it.
Find out if I need a slide accumulator. (This could be configured on the fly as slow belt.)
Is there a difference between an input conveyor and a spacing conveyors?
How does everything get mounted together?

pkrush, 2016-02-10:
The milestone changed so much I just closed the issue.

All Done:
*Try motor shield with 24v motor
*Solder 24v motors
*Guides need to be a little wider
*Connector plate:
*Bring the conveyors .5mm closer with the connector plate
	*Enlarge the outline by 2mm
*Motor Rail:
	Set up a new one for 380 motors:
	*Why? Make the radius bigger,
	*Different hole spacing & size
	*Larger bushing size.
	*Move the T-Screw back 2mm. (On the top plate as well.)
	*Move the foot down 2mm.

*Layout basic sizes and layout of conveyors and bins.
*As I work on it change the layer colors by material
*Make mount for bottom scanning camera

Closed 2016-02-10.

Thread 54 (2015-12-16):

At the end of the input conveyor put in a coin blocker

pkrush, 2015-12-16:
Physically only allow cents to go through and stop stacked coins.
Depending on how the coins are stacked this is going to jam.
Also non-pennies, bent, gunked, glued, gummed, etc coins will get stuck.
Sense current to know when the belt jams
To clear:
Run in reverse
Vibrate by running in both directions
I am think this is enough. It’s going to jam every so often and this is OK, it a low cost semi-auto system. The user can just clear it.
If it’s a huge issue maybe use solenoid to remove coins from belt.

pkrush, 2016-01-13:
Before I write software for this I need to try flexible flaps.

pkrush, 2016-01-28:
Flexible flaps work but I have not tried them much.
Putting the conveyor on an angle and stopping the motors for 20ms every 50ms works great for pulsing and shaking coins down.

Closed 2016-02-05.

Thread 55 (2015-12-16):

Add Slide Accumulator after DIY Hopper

pkrush, 2015-12-16:
**Slide Accumulator:**
A slide to buffer the varying output from the input feed.
I think the material is an open question. Delran? Acrylic? Waxed wood? Sheet metal?
Even a stock hopper would be benefit from an accumulator.
Put an IR sensor near the top of the slide. If it’s blocked slow or stop the feel belt.

**Why an Accumulator?**
This system has higher throughput when the coins are more uniformly spaced.
For a given camera & lighting setup there is a max speed of the imaging conveyor before the images get blurry.
The camera images the coins better with a slower belt.
A lower cost camera can be used with lower belt speeds.

pkrush, 2016-01-28:
Inline Conveyors at different speeds works great for a small amount of buffering. Putting an LED strip under the conveyors for backlighting looks like it would work great for adjusting speeds for metering. Also it looks cool!
There are so many great accumulator systems on youtube with vibration or belts that move in opposite directions, but they are so big.

pkrush, 2016-01-28:
I did try a 100mm long delren flat slide, but it was too long. It was just an empty conveyor body.
Try mini slides like this based on extending the guides past the end of the conveyors?

pkrush, 2016-02-03:
Going up hill and pulsing the conveyor motor causes the coins to slide. Tracking this with the backlight camera(or not...) gives the system enough accumulator effect for now.

Closed 2016-02-03.

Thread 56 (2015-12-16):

Clear Belt Imaging Conveyor

pkrush, 2015-12-16:
Sides only 19.1mm wide to make imaging easer.
Clear belt just to start using it. It will be needed later.

pkrush, 2016-01-13:
**Build another Imaging conveyor:**
First build another spacing conveyor and learn from that.
First task try a clear belt in the old one.
Triangle design so there is room for a camera under the belt, and the belt is each to change.
Motor is at the end, the point of the triangle.
3 bin design, 2 boxes and the drop off.
3 bins: copper, zinc, special & not confident.
Solenoid sorts to two 4x4x4 boxes so the conveyor needs to be 4” tall.
No light strip in this design
Guides and settle space before the camera and the IR sensor.
Solenoid plate should have locator tabs
IR sensor hole needs to be smaller, Test first. Make it 1mm, then drill?
Lift side rails above the IR sensor 0.5mm?

pkrush, 2016-02-10:
All Done:

The hopper and accumulator conveyors:
	*Both double length as before.
*Hooked together, motor to motor as one with the current base connectors.
*Both angle up the scanning conveyor.
*The angle will be adjustable, by putting a block/book under the end for now.
*Make standard motor end plates.
*Make an end plate filler when the conveyors are end to end.

Hopper conveyor:
*Change side rails to 42mm taller legs, rounded to change angles.
*Extend the side rails to form a hopper.
*Add another end plate on top

Accumulator conveyor:
*The drop off end needs to be on a -23.2 degree angle, so the base place will be angled.
*It will hook into the large scanning base plate with tabs with room to angle a bit.
	*Make an end plate without feet
*It needs to hook into base plate.

Scanning conveyor:
*Just make one to see how the belt runs.
*Cut and build it! Don’t wire every solenoid!

*100mm belt height.
	Under Camera:
	Usb100wo3m
		*6mm lens
		*80mm from bottom of board to top of belt
		*Usb connector on “bottom of image” /  motor side.
		*1.8mm thickness x 6mm holding area
*38.2mm
*12mm clearance under

*End at 463 Y
*Clear belt
*There will need something frosted, or paper to make the back lighting work better?
*Motor is at the drop off end.
*6 solenoids to 6 boxes.
*Solenoids every 60mm on alternating sides.
*Solenoid plates will be small and individual for each solenoid.
*Unwanted zincs will fall off the end into a bucket.

pkrush, 2016-02-11:
Closing to refocus the issue to:
Tune and rebuild 3 conveyor system (Hopper, Accumulator and Scanning)

Closed 2016-02-11.

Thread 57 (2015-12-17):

Portable Prototype Penny Sorter End Goal

pkrush, 2015-12-17:
This needs to be edited more, but its worth posting for now.

**Portable Prototype Penny Sorter End Goal**
Open source hardware & software system that is simple & easy to build.
That can be built for under $50 in parts in batches of 20 including shipping, special tool costs.
A bill of materials with prices & sources.
Frame, Cameras, Conveyors, Lights, solenoids, controls/ electronics, power supplies, etc, cables.
Sorts Lincoln pennies:
Average 7200 pennies an hour.
Quick-manual/semi-auto hopper/feeder
Into 10+ configurable bins.
Scanning both sides of the coin
Scanned flat, not rolling, on a belt or slide
Using stock and 3D printed and laser cut parts only.
Capable of sorting all Lincoln pennies 1909-2015 by date and mint mark.
ID’s designs of other common same sized cents
ID’s unknown coins as unknown. (Not Overfit)
That works independently on a Windows PC.
Image processing written in C++
Finds rotation and design transition errors.
Sorts by color, grade, and confidence.
That different 10 people have physically built it.
That 5 different developers have compiled it.
Scanning, classification, and sorting can be operated independently.
Software and hardware self-testing modes and tests written to ensure the system works.
Enclosed fixed lighting not affected by changes in ambient lighting.
Options to choose database to work out of, or create new one.

Tech How:
Some of these features are for development and can be in a hidden advanced mode.
Really there are many independent modules.

Why:
Why the specs?
- Arduino control
- 2+ redesigned solenoids leading to 3+ bins
- A slow belt & metering system replaces the coin hopper

How can this be different (Possible Options :)
Less:
Not hopper, one camera, No solenoid. No conveyor
More:
More than one system running in parallel
A stock hopper
Better cameras (Faster & higher resolution)
Move solenoids/bins
Embedded processing Unit.

See Future Milestones for coins and parts beyond pennies.

pkrush, 2016-02-05:
"Scanned flat, not rolling, on a belt or slide"
This is big deal. Rolling coins is how a coin accepter works and I think would be better for a mass produced system. This is too specialized to just coins. One reason I am designing this system with conveyors is because many different types of parts other then coins can used in the system.

Closed 2017-12-06.

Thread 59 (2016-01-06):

Get metering/better spacing on the new conveyors

pkrush, 2016-01-06:
Even an off the shelf coin hopper does not meter out the greatest. The better spaced the coins are the quicker and eaiser the system is.

It's important that such a system is not based on the size of a coin in hardware.

pkrush, 2016-01-13:
Build another spacing conveyor:
Build it upside down from past conveyors? Then the side rails would be the guides.
To meter and space the coins. No stacked coins with even spacing from an uneven input.
Better than a hopper because it cannot just handle a large range of coins sizes, but it can handle many types of small parts.
Controlled by a camera on top viewing outlines of the coins from the back lighting, LED lighting strip under the belt.
White Translucent 30x.15mm thick belt.
Make space for the lighting strip on bottom.
Angling up to the tall imaging conveyor.
Delron flaps to knock the doubled coins, but bends away so it does not cause a jam.
Go back to the blocker design, but mount a flap instead?
Or mount the flaps on tall side rail extensions.
Heck these flaps and speed increases should be enough.

This applies to the imaging conveyor as well:
Put a 2mm tall tap on top of the end plate to make them a fat cross.
Somehow I cut 3mm end plates mirrored, be careful next time.
Put clearance holes in the side rail to tighten the solenoid plate.
The motor axis can be moved 1mm down in Y.
Clearance for a light strip
Bigger holes for bushings.
Can the end plate be any wider to square the side rails more, .2mm wider?
Keep the old conveyor together.

pkrush, 2016-01-29:
**What is the spacing conveyor:**
To meter and space the coins. No stacked coins with even spacing from an uneven input.
Better than a hopper because it not only can it handle a large range of coins sizes, but it can handle many types of small parts.
Later: Controlled by a camera on top viewing outlines of the coins from the back lighting, LED lighting strip under the belt.
Flaps and speed increases might be enough and active spacing via webcam might not be needed.

Tasks (I did all of this already!):

This applies to the imaging conveyor as well:
*Keep the old conveyor together.
*Remove the IR sensor holes.
*Bigger holes for bushings.
*The motor axis can be moved 1mm down in Y.
*Make it 16mm longer:
*Change White Translucent 30x.15mm thick belt to 120mm Long, spaced for 4” boxes (4 3/8”))
*Design middle conveyors for a solenoid in the middle, but don’t install them.
*Put clearance holes in the side rail to tighten the solenoid plate.
*Put another screw on the motor plate, only used if there is no solenoid plate.
*Put guides back on, Delron
*End Plates:
*Put a 2mm tall tap on top of the end plate to make them a fat cross.
*Can the end plate be any wider to square the side rails more, .2mm wider?
*Clearance for a light strip
*Test cutting Delron
*Test cutting 3mm for 4# sheet metal screws
*Lots of holes for self-taping screws.
*Solenoid plate should have locator tabs
*Connect the conveyors with small base plates with locator tabs in side rails & end plates.

*Fix alignment on middle notch.
*Don’t cut the notch in the top plate for the solenoid.
*Document building it.
*Cut the parts.
*Build it
*Make and add a belt
*Cut and install the guide shims.

Fixes:
*Try just making washers for the shims
*Motor plate should have a 3mm foot.
*The motor side rail should have a 6x6mm tab, and the top plated should be notched.
*Make clearance holes bigger in the top plate
*Run on laser cut wood hole? 2.1mm? Why not? Carbon powder is a lube
*Wait: Drill out bushing holes with a #13 drill (I question if there is a better way!)
*Lift up the motor end plate 2mm under the coupling.
*Motor Side Rail should be notched for Solenoid plate
*Make Solenoid plate longer to notch into motor side rail again.
*Can I get the second hole set back on 20mm centers?
*Add last set of holes in top plate and notches in side rail
*Make the guide gap .8mm smaller.
*Make full guides on the next ones.

Fix:
* Motor rail notch is 1mm too high
*42mm shaft holes can be a tiny bit tighter.
*Guide clearance holes. Some bigger, some smaller.
*Make a spacing tool when installing the guides.
*The base plate needs to be bigger and screwed in.
*	Put t-slots in side rails.
*Make the end plate feet longer.
*Try bearings in one, bushings in another.
*6mm Layout:
Solenoid plate was cut upside down.
*Make more shim washers
*The guides need 3 screws because the top plate bows.
*Hook the 4 motors up to the shield.
*	Do a back and forth action on the first conveyor.

Fix Again:
Motor end plate:
*Make clearance for the base plate.
*Lower the feet 2mm
*Make full guide shims.
*Test ¼ mdf again.

Flat Accumulator Section:
All Parts the same as the conveyor but:
*	No motor or motor rail
*	No belt, or shafts
*	The guide shims are one piece with center section
*		It has a front extension that rides under the belt before
*	Guides on the conveyor before run to the back of the conveyor
*	Uses 2 end plates instead of one.

Closed 2016-02-10.

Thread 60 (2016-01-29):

Metering, spacing, and classification of mixed coin sizes

pkrush, 2016-01-29:
Currently CoinSorter only handles one size of coin at time with an off the shelf coin hopper. One should be able to handle mixed coin sizes with a series of independently driven conveyors controlled with an Arduino.  Handling mixed coin sizes would make the system much more useful. For example it could find rare coins while doing the simple act of sorting and counting mixed change. This might involve some mechanical changes to conveyor belt guides and fingers or some electronic changes such as adding IR or eddy current sensors.

Skills Needed: Arduino, OpenCV, C++, Python, SQL, image processing, machine learning, Caffe, convolutional neural networks, basic mechanical & robotics design

Closed 2017-12-06.

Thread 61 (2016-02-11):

Future Conveyor Ideas

pkrush, 2016-02-11:
More notching can be done in the designs to help with alignment.
Guide flaps are attachments so they can be worked on later:
Plastic guide flaps, maybe with tubing to knock the doubled coins, but bends away so it does not cause a jam. Delron works, but what else can be laser cut. Harder rubber?

A triangle design could still be the same shape, with rectangular side rails, and feet tabs in the side rails. It would have another idler under the motor shaft. No end plates on the main conveyor part, but there can be a 3mm or 6 mm bottom angled cross plate.

I have to spend some time with connectors, the right wire. This is unmanageable. I want the right color, right gage, and flexible wire. Maybe use a PCB?
Somehow make the top plate thicker and somehow put the belt around the end plates so the belt is super easy to change.
An inferred camera would be great to see if there is friction!

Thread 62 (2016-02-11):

Tune and rebuild 3 conveyor system (Hopper, Accumulator and Scanning)

pkrush, 2016-02-11:
Make the hopper bin plate
Finish all the guides.

Accumulator Conveyor:
Sand acrylic top plate and shorten the belt

Test it for 15 minutes by hand and an hour with the cube hopper
Dirty the belts
Get average speeds

Make mount for top scanning camera
Set up for the backlight camera:
Make base for the LED strip, or just widen connector plate?
Put LED strip under all the conveyors.
Make a mount for the backlight camera
Mount a few solenoids

Make a Base, 300x500mm sits on a large clear container
One of the boxes & base will have a hole along with the base for the coins to drop into the copper bin.

Try to take pictures at 72mm a second.

Later Re-Build another full 3 conveyor system:
There needs to be a way to route and mount wires.
Contain/mount the wires and electronics.
Make the rest of the 4x4x4-ish boxes
Make 2mm shaft holes smaller
Guides with slots to adjust for coin size.
Something went wrong with the top plate alignment and it was mirrored wrong when cut.

Scanner Side Rails:
	Change for 4mm shaft. Lower the motor.

After 2nd build:
.15mm thick belting would be better! Order .15 thick clear and satin 40mm? 30mm?
A clear join would be better!

End plates are off center slightly. Move it more off center, or center it.
The lighting and the camera can be a module:
That pulls out.
Or just added on the bottom!
Put a 1mm shoulder on the top plate by the motor.
Include the motor rail in the connector plate between the hopper and Accumulator. So this would be 130mm-ish wide.
Big hopper end plate
	Tab it.
	Move the screws to the corners
Make it symmetrical

Try making a bill of bill of materials

pkrush, 2016-02-15:
All Done:
*Finish all the guides.
Accumulator Conveyor:
*Sand acrylic top plate and shorten the belt (Works better sanded, as it does not stick)
*Put it together
*Tune it to 72mm a second:
It’s doing 8.8lbs in 10 minutes with the manual hopper (about 3 boxes an hour), this is about 2 coins a second.
Manual Hopper: 600 sec: 1089, 2.15 a second
Out of curiosity: Hand sort Test: 125 Sec: 2 1982, 15 copper, 50 zinc, 67 total, .536 a second

pkrush, 2016-02-15:
Today:  Refine the Scanning Conveyor:
Beef it up.
Make mount for top scanning camera:
Have the camera’s offset from each other.
Lift up side rails where there is no top plate so it can be covered by thick blue paper.
Go to a 258RPM motor(from 1000RPM)
	Change for 4mm shaft. Lower the motor.
Open the bottom camera side so I have access to the camera and lights
Cut a top plate correctly mirrored
Make base for the LED strip
Holes to mount the boards
Make 2mm shaft holes smaller:
The drop off should be thicker around the 2mm shaft.

pkrush, 2016-02-15:
Done:
Refine the Scanning Conveyor:
*Beef it up.
*Lift up side rails where there is no top plate so it can be covered by thick blue paper.
*Go to 258RPM motor
	*Change for 4mm shaft. Lower the motor.
*Open the bottom camera side so I have access to the camera and lights
*Flip the solenoids on the side rails.
*Make base for the LED strip
*Add holes to mount the boards
*Make 2mm shaft holes smaller:
*The drop off should be thicker around the 2mm shaft.
*Make holes for angled conveyor connector

pkrush, 2016-02-24:
Done for now. I need to take and post pictures of it!

Closed 2016-02-24.

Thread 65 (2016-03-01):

Design and build a 5 section coin sorter

pkrush, 2016-03-01:
**Go to a 5 section design:**

**Hopper:**
* Same as before, except make the angle less, like it was at e-week.

**Accumulator:**
* Same as before, except make the angle less, like it was at e-week.
* Maybe the accumulator is not needed, but the Hopper and Accumulator designs have been field tested and work great.

**Top scanner:**
* A simple short flat conveyor moving faster than the accumulator.
* Off the bin

**Bottom scanner:**
* A no belt accumulator mesh top plate section
* The bottom camera section should be off the bin and work with a 12mm camera.

**Sorter(s):**
* Same as the sorting section of the last scanning conveyor.
* You can add more sections to make this longer.
* They sit under the bin(s).

Why?:
No clear belt, so it’s thinner, easier to route, less pulleys, smaller motor, less parts, easier to wire and control for right now, because the motor will be the same. The 0.3mm thick clear belt is stickier and more difficuit to work with than 0.15mm thick frosted belt.
Smaller sections are better for laser cutting.

pkrush, 2016-03-02:
Now it's 4 sections. The cameras will bridge between two sectons.

Done:
*Get top camera mount designed
	*98.5mm from top plate to sensor side of the circuit board for a 12mm lens.
*Redesign same camera plate for top and bottom
*Redesign camera conveyor top plate

pkrush, 2016-03-04:
Done:
*build first conveyor
*New bottom plate
*Make side rails

**Next steps:**
Make guides
3mm Light bars that double as cross braces patch the two conveyors together.
Finish the other conveyor
	Solder last motor
Put T’s in top camera rails

pkrush, 2016-03-05:
Done:
*Make guides
*Finish the other conveyor
**It works!**

Next:
Solder last motor
Put T’s in top camera rails
Mount and test both cameras

pkrush, 2016-03-07:
Top and bottom camera view with ambient lighting (I need to put in the LED lighting)
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

pkrush, 2016-03-07:
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

pkrush, 2016-03-08:
Done:
*Mount bottom camera
*Solder last motor
*Put T’s in top camera rails
*Mount top camera
Next:
Add lighting
Hook up motor and lights to Arduino
Try it cube hopper

pkrush, 2016-03-10:
Done:
*Add lighting
*Try cube hopper

Arduino:
Output on the serial line at every cycle so the cameras know when to take the image.

Python:
Read the serial port
Time the capture of top and bottom images when the coins come to a stop

pkrush, 2016-03-10:
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

pkrush, 2016-03-16:
In general I am getting clear 1080x720 shots of the top and bottom simultaneously. This is cool.

**Done:**
*Output on the serial line at every cycle so the cameras know when to take the image.
*Tune the belt timing to take an image after the pennies come to a rest, but not before they start moving again.
*Maybe it would run better if the whole system was on a down angle?
	*Yep! It does work better angled down…

**Next:**
Clean up all the zincs and move to all copper
Scan 500 coins
Manual label these pre-scanned coins
Try finding centers in batch

pkrush, 2016-03-17:
**Get centers:**
It's working better
Ok I just saw one coin 18.96mm and another 19.14mm
**Done:**
* Clean up all the zincs and move to all copper
* Use a capacitor to stop the Arduino from auto-resetting on serial connection.
* Hook the LED’s up to a wall 12V source
* Hook the Hopper up to the 15V variable power supply (I’m running at low voltage, it needs a power boost every now and then.
* Why is the bottom camera going black every so often or account for it?
* Scan 500 coins

**Next:**
Manually label these pre-scanned coins
But don’t spend a lot of effort trying to calibrate the cameras to each other.
Try finding centers in batch

Closed 2016-08-30.

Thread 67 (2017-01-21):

Get the close up shots with a cheap camera

pkrush, 2017-01-21:
A cheap system might need to position the coin for microscope image captures. Positioning in x is easy as you just move the belt. Y, crossways is trickier.

**You have to turn the coin or move the camera:**
* Manually
* Random by running in the loop.
* A jerk motion on the belt that turns the coin in a fast motion and moves in slow motion.
* Move the camera back and forth.
* Move the conveyor
* Move the coin: two conveyors together can spin
* The conveyor can be on an angle and the coin spinning on a guide
* A rubber guide can turn the coin.
* The solenoid can turn it somehow.
* A motor under can pop up or from the side and turn the coin
* The conveyor can be on an angle and the coin rolls on a rubber guide to one side.

Closed 2017-12-06.

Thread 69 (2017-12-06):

Fixes to the current hardware

pkrush, 2017-12-06:
Mount the camera on the now 3mm side panels so it can be moved up and down. Make the 3mm side panel 6mm.
Camera side rails:
Move top led hole 2mm lower. Move the bottom one 1mm lower
Put cut outs in the wire holes.
Have one place for the EndMount.3dm file and make sure it’s the right one.

Closed 2020-10-11.

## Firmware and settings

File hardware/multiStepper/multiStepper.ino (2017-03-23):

// MultiStepper
// -*- mode: C++ -*-
//
// Control both Stepper motors at the same time with different speeds
// and accelerations. 
// Requires the AFMotor library (https://github.com/adafruit/Adafruit-Motor-Shield-library)
// And AccelStepper with AFMotor support (https://github.com/adafruit/AccelStepper)
// Public domain!

#include <AccelStepper.h>
#include <AFMotor.h>

int motor_speed = 350;
// two stepper motors one on each port
AF_Stepper motor1(48, 1);
AF_Stepper motor2(48, 2);

// you can change these to DOUBLE or INTERLEAVE or MICROSTEP!
// wrappers for the first motor!
void forwardstep1() {  
  motor1.onestep(FORWARD, DOUBLE);
}
void backwardstep1() {  
  // This is called with a speed of zero
  // There is no stop function in AccelStepper 
  //So this works great for stop if you only need on direction
  //  motor1.onestep(BACKWARD, DOUBLE);
}
// wrappers for the second motor!
void forwardstep2() {  
  motor2.onestep(FORWARD, DOUBLE);
}
void backwardstep2() {  
  // This is called with a speed of zero as there is no stop function
  // There is no stop function in AccelStepper 
  //So this works great for stop if you only need on direction
  //motor2.onestep(BACKWARD, DOUBLE);
}

// Motor shield has two motor ports, now we'll wrap them in an AccelStepper object
AccelStepper stepper1(forwardstep1, backwardstep1);
AccelStepper stepper2(forwardstep2, backwardstep2);

void setup()
{  
  pinMode(A5, INPUT);
  pinMode(A4, INPUT);
  stepper1.setSpeed(motor_speed);
  stepper1.runSpeed();
  stepper2.setSpeed(motor_speed);
  stepper2.runSpeed();
}

void loop()
{
  int run1 = 0;
  run1 = digitalRead(A5);

  int run2 = 0;
  run2 = digitalRead(A4);

  if (run1 == LOW)  {
      stepper1.setSpeed(motor_speed);
      stepper1.runSpeed();

    }
    else
    {
      stepper1.setSpeed(0);
      stepper1.runSpeed();
    }
      
    if (run2 == LOW) {
      stepper2.setSpeed(motor_speed);
      stepper2.runSpeed();
    }
    else
    {
      stepper2.setSpeed(0);
      stepper2.runSpeed();

    }
}

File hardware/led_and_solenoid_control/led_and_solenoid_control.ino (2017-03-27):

#include <Adafruit_NeoPixel.h>
#ifdef __AVR__
#include <avr/power.h>
#endif

#define SOLENOID_PIN       2
#define HOPPER_PIN       3
#define TOP_CONVEYOR_PIN       A4
#define BOTTOM_CONVEYOR_PIN       A5
#define LED_PIN            6
//LED_PIN8 is just because I did not want to solder...
#define LED_PIN8           5


// How many NeoPixels are attached to the Arduino?
#define NUMPIXELS      26

Adafruit_NeoPixel pixels = Adafruit_NeoPixel(NUMPIXELS, LED_PIN, NEO_GRB + NEO_KHZ800);
Adafruit_NeoPixel pixels8 = Adafruit_NeoPixel(8, LED_PIN8, NEO_GRB + NEO_KHZ800);

int delayval = 65; // delay for half a second
int old_pixel = 0;

void setup() {
  
  // This is for Trinket 5V 16MHz, you can remove these three lines if you are not using a Trinket
#if defined (__AVR_ATtiny85__)
  if (F_CPU == 16000000) clock_prescale_set(clock_div_1);
#endif
  // End of trinket special code
  Serial.begin(115200);
  pinMode(SOLENOID_PIN, OUTPUT);
  pinMode(HOPPER_PIN, OUTPUT);
  pinMode(TOP_CONVEYOR_PIN, OUTPUT);
  pinMode(BOTTOM_CONVEYOR_PIN, OUTPUT);
  digitalWrite(SOLENOID_PIN, LOW);
  digitalWrite(HOPPER_PIN, HIGH);
  digitalWrite(TOP_CONVEYOR_PIN, LOW);
  digitalWrite(BOTTOM_CONVEYOR_PIN, LOW);
  pixels.begin(); // This initializes the NeoPixel library.
  pixels.setPixelColor(0, pixels.Color(255,255,255));
  pixels.show();
  pixels8.begin(); // This initializes the NeoPixel library.
}

void loop() {
  if (Serial.available() > 0) {
    int input = Serial.parseInt();
    if (input < NUMPIXELS) {
      //for(int i=0;i < NUMPIXELS;i++){
      pixels.setPixelColor(old_pixel, pixels.Color(0,0,0));
      pixels.show();
      pixels.setPixelColor(input, pixels.Color(255,255,255));
      pixels.show();
      if (input > 17) {
        pixels8.setPixelColor(old_pixel-18, pixels8.Color(0,0,0));
        pixels8.show();
        pixels8.setPixelColor(input-18, pixels8.Color(255,255,255));
        pixels8.show();
      }
      old_pixel = input;
    } 
    if (input == 26) {
      pixels.setPixelColor(old_pixel, pixels.Color(0,0,0));
      pixels.show();
      for(int i=0;i < 18;i++){
      pixels.setPixelColor(i, pixels.Color(29,29,29));
      pixels.show();
      }
    } 
    if (input == 27) {
      for(int i=0;i < 18;i++){
      pixels.setPixelColor(i, pixels.Color(0,0,0));
      pixels.show();
      }
      for(int i=18;i < NUMPIXELS;i++){
      pixels.setPixelColor(i, pixels.Color(50,50,50));
      pixels.show();
      pixels8.setPixelColor(i-18, pixels8.Color(50,50,50));
      pixels8.show();
      }
    } 
    if (input == 28) {
      for(int i=18;i < NUMPIXELS;i++){
      pixels.setPixelColor(i, pixels.Color(0,0,0));
      pixels.show();
      pixels8.setPixelColor(i-18, pixels8.Color(0,0,0));
      pixels8.show();
      }
     
      pixels.setPixelColor(0, pixels.Color(255,255,255));
      pixels.show();
    } 
    if (input==100) {
      digitalWrite(SOLENOID_PIN, LOW);
    } 
    if (input==101) {
      digitalWrite(SOLENOID_PIN, HIGH);
    } 
    if (input==102) {
      digitalWrite(TOP_CONVEYOR_PIN, LOW);
    } 
    if (input==103) {
      digitalWrite(TOP_CONVEYOR_PIN, HIGH);
    } 
    if (input==104) {
      digitalWrite(BOTTOM_CONVEYOR_PIN, LOW);
    } 
    if (input==105) {
      digitalWrite(BOTTOM_CONVEYOR_PIN, HIGH);
    } 
    if (input==106) {
      //Sending the Hopper Pin low resets the hopper
      digitalWrite(HOPPER_PIN, LOW);
    } 
    if (input==107) {
      digitalWrite(HOPPER_PIN, HIGH);
    } 
    if (Serial.read() == '\n') {};
  }
}

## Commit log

2015-08-04 Set up a new solenoid and started tuning the timing.
2015-08-05 Tuned solenoid timing and de-skewed images
    De-Skewed image from standard photo snapshot to Liveview switch.
2015-08-05 Added Curl Call to digits.
    It barely works. But... The system was working as a whole physically
    sorting coins for the first time.
    It looks like the fileWatcher thread is dying and there is timing issues
    now that the digits look up is in place. This needs to be one program,
    all in C#, instead of two, and not saving the images to disk.
2015-08-11 More Stable Sorting
    Slowed the initial capture rate
    Move the camera back to give more time for the solenoid.
    Added more labels/categories to model.
2015-08-12 Added current proof of concept performance
2015-08-24 Added Hardware Documentation
    [25mmMotor.3dm, D-Bushing.3dm, GearboxBracket3.3dm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]
2015-08-24 Added Actuators Doc
2015-09-25 Add Arduino class
2015-10-05 Added IR Sensor
2015-10-07 IR sensor working, added counter
2015-10-09 Ardunio Actuator Start
2015-10-15 Actuator with IR Sensor working.
2015-10-16 Moved Camera to End of Belt
2015-10-22 Removed: VB, MATLAB, Canon EOS, HP
    Removed: VB, Matlab, Canon EOS, HP Power supply Drivers
    Almost replaced with C#, OpenCV, webcam, Arduino Control
2015-10-29 Added Webcam camera settings
2015-11-09 Labeling Dates
    [coinAcceptor.3dm, coinAcceptor.dxf]
2015-11-17 Live Classify, no Belt
    [32.5.dxf, TestHoles.dxf, frameTopTest.3dm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]
2015-11-17 Added Powerpoint
2015-12-04 Laser Cut Paper Iris on Web Cam
    [paperIris.3dm, paperIris.dxf]
2015-12-29 In the middle of designing new conveyors
    [0.2mm.dxf, 25mmMotor.3dm, 3mm.dxf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]
2016-01-07 First Direct DC Motor Conveyor Build
    [3mm.dxf, 6mm.dxf, OldMotorEnd.3dm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]
2016-01-08 Conveyor with Solenoid
    [endMount.3dm, englishTest.3dm]
2016-01-16 Building dnn module
    [endMount.3dm]
2016-01-19 Conveyor Updates
    [3WaySolenoidTopPlate.3dm, endMount.3dm]
2016-01-20 Conveyor Changes
    [endMount.3dm]
2016-01-21 Conveyor update
    [endMount.3dm]
2016-01-26 More Conveyor Updates
    [endMount.3dm]
2016-02-04 Broke out Scanner Types in Rhino3D File
    [endMount.3dm, scanning.3dm]
2016-02-10 Scanning Conveyor Updates
    [endMount.3dm]
2016-02-10 Revert "Scanning Conveyor Updates"
    This reverts commit f132f9496b110309c3ca125fb8f194adacf8a1b5.
    [endMount.3dm]
2016-02-10 Revert "Revert "Scanning Conveyor Updates""
    This reverts commit 145c3f34e5cf82c07226a5b994a644242391b4c5.
    [endMount.3dm]
2016-02-16 scanning conveyor rebuild
    [3mm.dxf, 6mm.dxf, endMount.3dm]
2016-02-16 made baseplate
    [6mm.dxf, endMount.3dm]
2016-02-19 Added lower camera mount
    [1.5mm.dxf, 3mm.dxf, 6mm.dxf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]
2016-02-19 Scanner Guides
    [1.5mm.dxf, 3mm.dxf, 6mm.dxf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]
2016-03-02 English Toy Testing.
    [0.2mm.dxf, 2mm.dxf, 3mm.dxf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]
2016-03-02 Added Top Camera Mount
    [2mm.dxf, 3mm.dxf, 6mm.dxf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]
2016-03-04 feeder conveyor updates.
    [2mm.dxf, 3mm.dxf, 6mm.dxf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]
2016-03-08 Top camera mounted
    [2mm.dxf, 3mm.dxf, 6mm.dxf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]
2016-03-10 Top Camera Mounting
    [0.2mm.dxf, 2mm.dxf, 3mm.dxf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]
2016-03-14 2 camera Cropping
    [0.2mm.dxf]
2016-05-18 Added Scanner Photos
    [3mm.dxf]
2016-08-18 HoughCircles works pretty good for 2 camera
2016-09-14 Added Stepper code
2016-09-14 Added unipolar Stepper code
2017-01-04 Done: Manually put on guides. Done: Detect the coin centers Done: Get crops while the belt is moving. Done: Save the images
2017-01-27 added 2 belt control for twirling coins for close up top and bottom camera captures
2017-02-22 added 2-arduino-enclosure
    [2-arduino-enclosure.dxf]
2017-02-22 Moved enclosure file
    [2-arduino-enclosure.dxf]
2017-02-22 Mirrored Holes
    [2-arduino-enclosure.dxf]
2017-02-28 Clean up
    [0.2mm.dxf, 1.5mm.dxf, 2-arduino-enclosure.dxf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]
2017-03-03 Changed Base Plate for conveyor
    [base-plate.dxf]
2017-03-09 Added Flip conveyor files
    [6mm.dxf, clear-control-cover.dxf, motor-rail-25by-stepper.dxf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]
2017-03-10 Added Second Conveyor, Flip, and Camera files
    [camera-cover.dxf, camera-cover2.dxf, camera-guide-washers.dxf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]
2017-03-14 Added Camera
    [camera-cover3.dxf, camera-mounting-plate2.dxf]
2017-03-15 Both conveyors are running
2017-03-22 Got conveyors running at different speeds
2017-03-27 Now you reset the hopper to dispense a coin.
    [led_and_solenoid_control.ino]
2017-11-07 Very large repo clean up was done. 195 files are being deleted and are few a being moved around.
    [0.2mm.dxf, 1.5mm.dxf, 25mmMotor.3dm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]
